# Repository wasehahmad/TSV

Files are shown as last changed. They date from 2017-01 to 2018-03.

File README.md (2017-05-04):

# TSV
Tractive System Voltage

This repository contains hardware and software for the PacMan (Pack Manager) and the AMS (Accumulator Management System)

Backup_pacman_software contains the software from the end of the 2016 project.

stable_software_20170413 contains the software on the packs at the end of the spring 2017 semester.

New_Pacman_Software contians the most recently tested software, with improvements added on to the stable_software.
Improvements include updated configuration parameters menus, power saving mode, and a lock mode that disables configutation
parameters to be edited.

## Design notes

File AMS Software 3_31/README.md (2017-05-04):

# LFEV Accumulator Mangement System (AMS)
This document describes the I2C interface to the AMS firmware, including the provided
functionality as well as how to test the boards outside of the pack. Also included is a brief
overview of how the software operates. 

## AMS I2C Interface

The following table describes the available functions in the current firmware revision.  
Included in the table is the command code as well as the I2C message structure:

### Command Code Description
| COMMAND | ENUM | DESCRIPTION |
|---|---|---|
| RESET_BY | 0x00 | Resets the bypass timer |
| SET_BY | 0x01 | Place device in bypass mode |
| PANIC | 0x02 | Rapidly blink LED |
| RELAX | 0x03 | End panic mode |
| SET_ADDR | 0x04 | Set device I2C address |
| SET_BYTIME | 0x05 | Set the bypass time |
| SET_V_CAL | 0x06 | Set the voltage calibration data |
| SET_SERIAL | 0x07 | Set the serial number |
| CHANGE_READ_TYPE  | 0x30 | Change the read type |

### API Documentation
#### RESET_BY: 0x00
This command resets the bypass timer within the device. If the bypass timer is not
reset before it counts up to the bypass limit, the device will begin discharging the battery in
bypass mode.
#### SET_BY: 0x01
This command directly sets the device into bypass mode.
PANIC: 0x02
This command sets the panic flag in the device. The panic flag does nothing more
than blink the “ACT” LED rapidly. None of the device functionality is affected.
#### RELAX: 0x03
This command disables the panic flag.

#### SET_ADDR: 0x04
This command sets the I2C address. The command word MUST be followed by
another byte to be set as the address. If this byte is not sent, the device can hang.

#### SET_BYTIME: 0x05
This command sets the bypass time limit for the device. The command word must be
followed by 2 bytes to act as the bypass time limit. These bytes must be sent MSB first. The
bypass time limit will be set to the given value multiplied by 32.8ms.
Reading data from the device:
To retrieve data from the device, an I2C read must be initiated for exactly 4 bytes. If
fewer or more bytes are read, the device can hang. The device will return two 16 bit values
representing the voltage and temperature respectively. The values will be transmitted MSB
first.

#### SET_V_CAL : 0x06
This command writes the calibration data to the AMS board's EEPROM. Four bytes of data 
should follow this command, two bytes for the slope, and two bytes for the offset. The 
high byte of the slope is sent first then the lower byte and the same process for the offset.

#### SET_SERIAL : 0x07
This command sets the 4-digit serial number for the AMS board. Four bytes of data should follow this 
command. Each digit in the serial number is sent individually beginning with the first digit.

#### CHANGE_READ_TYPE : 0x30
This command changes the read type for the AMS board. The board supports 4 different i2c reads. This 
command should be followed by another byte that dictates which read is to be performed: 
* for voltage/temp reading the next byte should be 0x00. 
* For the serial 0x01. 
* For the calibration data 0x02. 
* For the magic number 0x03.

## Device Programming and Testing
**The below guide has not been tested with the new version of the AMS software. It is recommended to connect
the AMS board to the Verifcation Unit for testing.**

To Program and test a device, you need a power supply capable of outputting at least
3 volts and 25 mA, a “PICKIT 3” programmer, and an “I2C2PC” adapter. A computer will be
needed with the PICKIT 3 software and RealTerm installed.
1. Attach the PICKIT 3 programmer to the AMS board.
2. Connect the AMS board to the power supply.
AMS Firmware Guide
3. Set the power supply to 3.3 volts with a limit of 1 A.
4. Enable power supply output. The voltage should settle to near 26mA.
AMS Firmware Guide
5. Connect the I2C2PC adapter to the I2C bus on the AMS board.
a. NOTE: The cable has been know to have connection issues. It may be necessary to check
the line voltage with an oscilloscope to ensure it can communicate with the bus.
6. Start PICKIT 3.
a. Select the file from the import dialog.
AMS Firmware Guide
b. Once the file has been imported, write it to the device.
7. Start RealTerm.
a. In the “Port” tab, select the I2C2PC adapter as the port (port 12, in this case).
b. Click “Change” to apply the change of settings.
8. Test basic I2C functionality by sending byte 0x00to address 0x04. The “ACT” LED
should blink once when the command is received.
AMS Firmware Guide
9. To test bypass mode, first increase the current limit of the power supply to 3A. This
time, send the packet 0x01.
a. The red “BYP” LED should light up and the current draw should increase to
2.9A.
b. Resend packet 0x00or reset the device to end bypass mode
10. Test the SET_ADDR command by sending the byte 0x04followed by the new I2C
address (here, it is 0x06) to change the address.
AMS Firmware Guide
a. Confirm the change in address by reading the EEPROM data in PICKIT 3
b. The data stored in location 0x00is the I2C address
11. Test the data retrieval by reading back 4 bytes from the device. The returned data
should reflect different voltage values if the supply voltage is changed between
iterations of this test.

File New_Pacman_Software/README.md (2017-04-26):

Lafayette College Formula Electric Vehicle

Pacman Software

This software controls the AT90CAN32 microcontroller located in the Lafayette Formula Electric Vehicle battery packs.  It is written in C and is built on AtomThreads RTOS.

The current version is v0.16 and has last been revised during the spring 2017 semester; the point of contact for this revision of software is Martin Townley.
Previous contributors to this software include Preston Bejabang and Geoff Nudge.

For documentation on this software, how to build and run it, the user manual and maintenace manual, please see http://sites.lafayette.edu/ece492-sp17/subsystems/tsv/

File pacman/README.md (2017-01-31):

# LFEV Pack Manager Main Board

## Overview

This directory contains the design of the LFEV "Packman" board. The "Packman" board, or
Pack Manager Board is responsible for monitoring the cells in the LFEV battery pack. This 
system contains a small AVR microprocessor capable of communicating high level data to the
SCADA system, while monitoring the pack for faults, managing cell charge/discharge, and tracking
the pack state of charge. This directory contains the PCB schematic and board layout
of the system.

## What's Here?

 - Kicad Project
     - Schematics
     - Board Layouts
     - Bill of Materials
 - Gerber Files
 - PDF Schematic

### Directory Structure

1. `Pacman_Rev_0_8` -- Contains versions of the finalized board layout, send these for fabrication
2. `project` -- KiCad project files... Open these to change the board design

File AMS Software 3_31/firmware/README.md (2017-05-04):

# AMS Firmware
Lafayette Formula Electric Vehicle Accumulator Mangement System Software

## Overview
This repository contains the PICLF1827 firmware. 

## Software Requirements
**OPTION A (Recommended)**
- Oracle VirtualBox

**OPTION B**
- MPLABX IDE 2.x or earlier
- MicroChip XC8 Compiler

### OPTION B: Oracle VirtualBox
The recommended way of building the system image is to use the pre-built VirtualBox environment. You will need to download VirtualBox, which can be found [here](https://www.virtualbox.org/wiki/Downloads).  

Go to the downloads page of the AMS repository, and download the latest virtual machine image. This image contains LXLE Ubuntu, and the MPLABX IDE and XC8 Compiler already installed. Simply mount the project folder on your host machine, and enable USB passthrough of the PICkit3 device.

### OPTION B: MicroChip MPLABX
This project was created using MicroChip proprietary IDE MPLABX. You can download a version of this IDE from [here](www.microchip.com/mplabx). However it should be noted that issues the PICkit3 and version 3.0 of the IDE may prevent programming of the PIC. A downgrade to version 2.x was required to successfully upload the software image.  
  
You will also need the MicroChip XC8 Compiler, which can be downloaded [here](www.microchip.com/compilers).

### Potential Problems
1. The PICkit3 has trouble with the MPLABX 3.x IDE, it complains that the firmware on the device is too old. Attempting to update the firmware either in the latest IDE, or an older one does not appear to have any effect.
2. If you are using the Virtual Machine Method, you must enable a USB Filter. Simply selecting Devices->USB Devices->PICkit3 is not enough. The PICkit3 re-uploads its firmware image upon each code upload. This causes the device to disconnect and re-connect itself. If a USB filter is not used, the host will take control of the PICkit3 immediately after it disconnects itself.

## Hardware Requirements
- PICkit3 Programmer

The PICkit3 Programmer is used to upload software images to the AMS microcontroller. The programmer can be purchased from MicroChip [Here](www.microchip.com/pickit3).

## Building the Image
Open MPLABX, click build... you're done

## Uploading the Image
Open MPLAB, click build, click program device... it should upload

If it did not upload verify that you have USB

##Additional Resources
Listed below are some additional resources for writing software for the AMS PIC.

### Power Saving Techniques
[PIC Microcontroller Low Power Techniques](http://ww1.microchip.com/downloads/en/DeviceDoc/01146B_chapter%202.pdf)

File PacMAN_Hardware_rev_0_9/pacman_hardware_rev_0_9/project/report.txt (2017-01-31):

Info: Reading netlist file "/home/strong/Documents/ECE492/pacman/pacman/hardware/main-board/project/pacman-main.net".

Info: Using references to match components and footprints.

* Warning: component 'T1': board footprint 'w_smd_inductors:transf_smd_ep7-8', netlist footprint 'custom_footprints:trans_flyback_LT8302'

* Warning: component 'Q2': board footprint 'w_smd_trans:sot23', netlist footprint 'custom_footprints:sot346'

* Warning: component 'Q1': board footprint 'w_smd_trans:sot23', netlist footprint 'custom_footprints:sot346'

* Warning: component 'U4': board footprint 'w_smd_dil:so-8', netlist footprint 'custom_footprints:msop_10_ads1015'

* Warning: component 'U5': board footprint 'Housings_SSOP:MSOP-10_3x3mm_Pitch0.5mm', netlist footprint 'custom_footprints:msop_10_ads1015'

* Warning: component 'D6': board footprint 'w_smd_diode:do214ac', netlist footprint 'custom_footprints:do214ac'

* Warning: component 'D5': board footprint 'w_smd_diode:do214ac', netlist footprint 'custom_footprints:do214ac'

* Warning: component 'D7': board footprint 'w_smd_diode:do214ac', netlist footprint 'custom_footprints:do214ac'

* Warning: component 'D8': board footprint 'w_smd_diode:do214ac', netlist footprint 'custom_footprints:do214ac'

* Warning: component 'D9': board footprint 'w_smd_diode:do214ac', netlist footprint 'custom_footprints:do214ac'

* Warning: component 'D18': board footprint 'w_smd_diode:do214ac', netlist footprint 'custom_footprints:do214ac'

* Warning: component 'D19': board footprint 'w_smd_diode:do214ac', netlist footprint 'custom_footprints:do214ac'

* Warning: component 'D15': board footprint 'w_smd_diode:do214ac', netlist footprint 'custom_footprints:do214ac'

* Warning: component 'X1': board footprint 'w_crystal:crystal_smd_5x3.2mm', netlist footprint 'custom_footprints:crystal_TXC_7A'

* Warning: component 'U13': board footprint 'w_smd_trans:tsot-6', netlist footprint 'custom_footprints:TLP2361'

* Warning: component 'SW1': board footprint 'w_switch:smd_push', netlist footprint 'custom_footprints:SW_RACON_8'

* Warning: component 'U10': board footprint 'w_smd_dil:mdip_6', netlist footprint 'custom_footprints:DCK'

* Warning: component 'R3': board footprint 'w_smd_resistors:r_0603', netlist footprint 'custom_footprints:CSNL1206'

* Warning: component 'F1': board footprint 'w_smd_resistors:r_1210', netlist footprint 'custom_footprints:C1Q'

* Warning: component 'P1': board footprint 'Connector_Molex_SL:molex_sl_smd_90_2', netlist footprint 'custom_footprints:AMPCONN_4POS'

* Warning: component 'U2': board footprint 'w_smd_trans:sot23-5', netlist footprint 'TO_SOT_Packages_SMD:SOT-23-5'

* Warning: component 'U9': board footprint 'w_smd_trans:sot223', netlist footprint 'TO_SOT_Packages_SMD:SOT-223'

* Warning: component 'R20': board footprint 'w_smd_resistors:r_0805', netlist footprint 'Resistors_SMD:R_0805_HandSoldering'

* Warning: component 'R19': board footprint 'w_smd_resistors:r_0805', netlist footprint 'Resistors_SMD:R_0805_HandSoldering'

* Warning: component 'R18': board footprint 'w_smd_resistors:r_0805', netlist footprint 'Resistors_SMD:R_0805_HandSoldering'

* Warning: component 'R25': board footprint 'w_smd_resistors:r_0805', netlist footprint 'Resistors_SMD:R_0805_HandSoldering'

* Warning: component 'R4': board footprint 'w_smd_resistors:r_0603', netlist footprint 'Resistors_SMD:R_0603_HandSoldering'

* Warning: component 'R30': board footprint 'w_smd_resistors:r_0603', netlist footprint 'Resistors_SMD:R_0603_HandSoldering'

* Warning: component 'R32': board footprint 'w_smd_resistors:r_0603', netlist footprint 'Resistors_SMD:R_0603_HandSoldering'

* Warning: component 'R31': board footprint 'w_smd_resistors:r_0603', netlist footprint 'Resistors_SMD:R_0603_HandSoldering'

* Warning: component 'R7': board footprint 'w_smd_resistors:r_0603', netlist footprint 'Resistors_SMD:R_0603_HandSoldering'

* Warning: component 'R6': board footprint 'w_smd_resistors:r_0603', netlist footprint 'Resistors_SMD:R_0603_HandSoldering'

* Warning: component 'R5': board footprint 'w_smd_resistors:r_0603', netlist footprint 'Resistors_SMD:R_0603_HandSoldering'

* Warning: component 'R37': board footprint 'w_smd_resistors:r_0603', netlist footprint 'Resistors_SMD:R_0603_HandSoldering'

* Warning: component 'R38': board footprint 'w_smd_resistors:r_0603', netlist footprint 'Resistors_SMD:R_0603_HandSoldering'

* Warning: component 'R23': board footprint 'w_smd_resistors:r_0603', netlist footprint 'Resistors_SMD:R_0603_HandSoldering'

* Warning: component 'R9': board footprint 'w_smd_resistors:r_0603', netlist footprint 'Resistors_SMD:R_0603_HandSoldering'

* Warning: component 'R24': board footprint 'w_smd_resistors:r_0603', netlist footprint 'Resistors_SMD:R_0603_HandSoldering'

* Warning: component 'R35': board footprint 'w_smd_resistors:r_0603', netlist footprint 'Resistors_SMD:R_0603_HandSoldering'

* Warning: component 'R36': board footprint 'w_smd_resistors:r_0603', netlist footprint 'Resistors_SMD:R_0603_HandSoldering'

* Warning: component 'R8': board footprint 'w_smd_resistors:r_0603', netlist footprint 'Resistors_SMD:R_0603_HandSoldering'

* Warning: component 'R14': board footprint 'w_smd_resistors:r_0603', netlist footprint 'Resistors_SMD:R_0603_HandSoldering'

* Warning: component 'R17': board footprint 'w_smd_resistors:r_0603', netlist footprint 'Resistors_SMD:R_0603_HandSoldering'

* Warning: component 'R16': board footprint 'w_smd_resistors:r_0603', netlist footprint 'Resistors_SMD:R_0603_HandSoldering'

* Warning: component 'R10': board footprint 'w_smd_resistors:r_0603', netlist footprint 'Resistors_SMD:R_0603_HandSoldering'

* Warning: component 'R34': board footprint 'w_smd_resistors:r_0603', netlist footprint 'Resistors_SMD:R_0603_HandSoldering'

* Warning: component 'R2': board footprint 'w_smd_resistors:r_0603', netlist footprint 'Resistors_SMD:R_0603_HandSoldering'

* Warning: component 'R15': board footprint 'w_smd_resistors:r_0603', netlist footprint 'Resistors_SMD:R_0603_HandSoldering'

* Warning: component 'R13': board footprint 'w_smd_resistors:r_0603', netlist footprint 'Resistors_SMD:R_0603_HandSoldering'

* Warning: component 'R1': board footprint 'w_smd_resistors:r_0603', netlist footprint 'Resistors_SMD:R_0603_HandSoldering'

* Warning: component 'D3': board footprint 'w_smd_leds:Led_0603', netlist footprint 'LEDs:LED_0603'

* Warning: component 'D12': board footprint 'w_smd_leds:Led_0603', netlist footprint 'LEDs:LED_0603'

* Warning: component 'D2': board footprint 'w_smd_leds:Led_0603', netlist footprint 'LEDs:LED_0603'

* Warning: component 'D1': board footprint 'w_smd_leds:Led_0603', netlist footprint 'LEDs:LED_0603'

* Warning: component 'U3': board footprint 'w_smd_dil:soic-16', netlist footprint 'Housings_SOIC:SOIC-16_7.5x10.3mm_Pitch1.27mm'

* Warning: component 'P4': board footprint 'w_conn_strip:vasch_strip_8x2', netlist footprint 'Connect:IDC_Header_Straight_16pins'

* Warning: component 'C16': board footprint 'w_smd_cap:c_elec_6.3x7.7', netlist footprint 'Capacitors_SMD:c_elec_6.3x7.7'

* Warning: component 'C10': board footprint 'w_smd_cap:c_elec_10x10', netlist footprint 'Capacitors_SMD:c_elec_10x10'

* Warning: component 'C11': board footprint 'w_smd_cap:c_1210', netlist footprint 'Capacitors_SMD:C_1210_HandSoldering'

* Warning: component 'C15': board footprint 'w_smd_cap:c_1210', netlist footprint 'Capacitors_SMD:C_1210_HandSoldering'

* Warning: component 'C9': board footprint 'w_smd_cap:c_1210', netlist footprint 'Capacitors_SMD:C_1210_HandSoldering'

* Warning: component 'C14': board footprint 'w_smd_cap:c_0805', netlist footprint 'Capacitors_SMD:C_0805'

* Warning: component 'C2': board footprint 'w_smd_cap:c_0603', netlist footprint 'Capacitors_SMD:C_0603_HandSoldering'

* Warning: component 'C18': board footprint 'w_smd_cap:c_0603', netlist footprint 'Capacitors_SMD:C_0603_HandSoldering'

* Warning: component 'C12': board footprint 'w_smd_cap:c_0603', netlist footprint 'Capacitors_SMD:C_0603_HandSoldering'

* Warning: component 'C21': board footprint 'w_smd_cap:c_0603', netlist footprint 'Capacitors_SMD:C_0603_HandSoldering'

* Warning: component 'C8': board footprint 'w_smd_cap:c_0603', netlist footprint 'Capacitors_SMD:C_0603_HandSoldering'

* Warning: component 'C20': board footprint 'w_smd_cap:c_0603', netlist footprint 'Capacitors_SMD:C_0603_HandSoldering'

* Warning: component 'C19': board footprint 'w_smd_cap:c_0603', netlist footprint 'Capacitors_SMD:C_0603_HandSoldering'

* Warning: component 'C7': board footprint 'w_smd_cap:c_1210', netlist footprint 'Capacitors_SMD:C_0603_HandSoldering'

* Warning: component 'C13': board footprint 'w_smd_cap:c_0603', netlist footprint 'Capacitors_SMD:C_0603_HandSoldering'

* Warning: component 'C17': board footprint 'w_smd_cap:c_0603', netlist footprint 'Capacitors_SMD:C_0603_HandSoldering'

* Warning: component 'C1': board footprint 'w_smd_cap:c_0603', netlist footprint 'Capacitors_SMD:C_0603_HandSoldering'

* Warning: component 'C4': board footprint 'w_smd_cap:c_0603', netlist footprint 'Capacitors_SMD:C_0603_HandSoldering'

* Warning: component 'C6': board footprint 'w_smd_cap:c_0603', netlist footprint 'Capacitors_SMD:C_0603_HandSoldering'

* Warning: component 'C3': board footprint 'w_smd_cap:c_0603', netlist footprint 'Capacitors_SMD:C_0603_HandSoldering'

* Warning: component 'C5': board footprint 'w_smd_cap:c_0603', netlist footprint 'Capacitors_SMD:C_0603_HandSoldering'

* Warning: component 'C23': board footprint 'w_smd_cap:c_0603', netlist footprint 'Capacitors_SMD:C_0603_HandSoldering'

* Warning: component 'C22': board footprint 'w_smd_cap:c_0603', netlist footprint 'Capacitors_SMD:C_0603_HandSoldering'

Info: Checking netlist component footprint "C1:/5572610D:Capacitors_SMD:C_0603_HandSoldering".

Info: Checking netlist component footprint "C2:/557225A0:Capacitors_SMD:C_0603_HandSoldering".

Info: Checking netlist component footprint "C3:/5572D9B1:Capacitors_SMD:C_0603_HandSoldering".

Info: Checking netlist component footprint "C4:/55726574:Capacitors_SMD:C_0603_HandSoldering".

Info: Checking netlist component footprint "C5:/5572DAEA:Capacitors_SMD:C_0603_HandSoldering".

Info: Checking netlist component footprint "C6:/55727969:Capacitors_SMD:C_0603_HandSoldering".

Info: Checking netlist component footprint "C7:/560A91B4/56DA9A93:Capacitors_SMD:C_0603_HandSoldering".

Info: Checking netlist component footprint "C8:/5574E706/561A469B:Capacitors_SMD:C_0603_HandSoldering".

Info: Checking netlist component footprint "C9:/5574E706/5574EF4E:Capacitors_SMD:C_1210_HandSoldering".

Info: Checking netlist component footprint "C10:/5574E706/56149C59:Capacitors_SMD:c_elec_10x10".

Info: Checking netlist component footprint "C11:/5574E706/560E8698:Capacitors_SMD:C_1210_HandSoldering".

Info: Checking netlist component footprint "C12:/5574E706/5574EF55:Capacitors_SMD:C_0603_HandSoldering".

Info: Checking netlist component footprint "C13:/5574E706/559EAEEF:Capacitors_SMD:C_0603_HandSoldering".

Info: Checking netlist component footprint "C14:/5574E706/561A342C:Capacitors_SMD:C_0805".

Info: Checking netlist component footprint "C15:/5574E706/560EA637:Capacitors_SMD:C_1210_HandSoldering".

Info: Checking netlist component footprint "C16:/5574E706/5574EF8D:Capacitors_SMD:c_elec_6.3x7.7".

Info: Checking netlist component footprint "C17:/5574E706/559EB3D2:Capacitors_SMD:C_0603_HandSoldering".

Info: Checking netlist component footprint "C18:/5574E706/5574EFA4:Capacitors_SMD:C_0603_HandSoldering".

Info: Checking netlist component footprint "C19:/561EAC87/561EE3E1:Capacitors_SMD:C_0603_HandSoldering".

Info: Checking netlist component footprint "C20:/560D7137/560D7928:Capacitors_SMD:C_0603_HandSoldering".

Info: Checking netlist component footprint "C21:/560D7137/560D79A3:Capacitors_SMD:C_0603_HandSoldering".

Info: Checking netlist component footprint "C22:/5574E706/56251D56:Capacitors_SMD:C_0603_HandSoldering".

Info: Checking netlist component footprint "C23:/5574E706/56252980:Capacitors_SMD:C_0603_HandSoldering".

Info: Checking netlist component footprint "C24:/5574E706/56C84061:Capacitors_SMD:C_0603_HandSoldering".

Info: Checking netlist component footprint "D1:/5572956F:LEDs:LED_0603".

Info: Checking netlist component footprint "D2:/557296B7:LEDs:LED_0603".

Info: Checking netlist component footprint "D3:/55735E6E:LEDs:LED_0603".

Info: Checking netlist component footprint "D5:/5574E706/5614A4E6:custom_footprints:do214ac".

Info: Checking netlist component footprint "D6:/5574E706/560E9E47:custom_footprints:do214ac".

Info: Checking netlist component footprint "D7:/5574E706/561A26BD:custom_footprints:do214ac".

Info: Checking netlist component footprint "D8:/5574E706/561F00F0:custom_footprints:do214ac".

Info: Checking netlist component footprint "D9:/5574E706/561F2090:custom_footprints:do214ac".

Info: Checking netlist component footprint "D12:/560A91B4/560D901A:LEDs:LED_0603".

Info: Checking netlist component footprint "D15:/560D7137/5618023D:custom_footprints:do214ac".

Info: Checking netlist component footprint "D18:/560A91B4/562AB319:custom_footprints:do214ac".

Info: Checking netlist component footprint "D19:/560A91B4/562B02FC:custom_footprints:do214ac".

Info: Checking netlist component footprint "D20:/5574E706/56C84F96:footprints:sod123".

Info: Checking netlist component footprint "D21:/560A91B4/56C97FC6:custom_footprints:do214ac".

Info: Checking netlist component footprint "F1:/5574E706/56D7F3E2:custom_footprints:C1Q".

Info: Checking netlist component footprint "J1:/5623433E/56153025:custom_footprints:conn_usb_B".

Info: Checking netlist component footprint "J2:/5623433E/56260A54:Connect:DB37FD".

Info: Checking netlist component footprint "J3:/5623433E/56CD8443:custom_footprints:MOLEX_RJ11".

Info: Checking netlist component footprint "L1:/5574E706/560E9174:Inductors:SELF-WE-TPC_M".

Info: Checking netlist component footprint "P1:/5623433E/56D7CCD6:custom_footprints:AMPCONN_4POS".

Info: Checking netlist component footprint "P2:/5623433E/562C320E:Connector_Molex_SL:molex_sl_smd_90_2".

Info: Checking netlist component footprint "P3:/5623433E/56151585:Connector_Molex_SL:molex_sl_smd_90_6".

Info: Checking netlist component footprint "P4:/5623433E/5623747B:Connect:IDC_Header_Straight_16pins".

Info: Checking netlist component footprint "P5:/5623433E/5615226C:Connector_1-27mm:JTAG_10ARM".

Info: Checking netlist component footprint "Q1:/560A91B4/562ABB38:custom_footprints:sot346".

Info: Checking netlist component footprint "Q2:/560A91B4/56D1463E:custom_footprints:sot346".

Info: Checking netlist component footprint "Q3:/560A91B4/56D0EFAD:custom_footprints:sot346".

Info: Checking netlist component footprint "Q4:/5574E706/56DA35B2:custom_footprints:sot346".

Info: Checking netlist component footprint "R1:/561E7314:Resistors_SMD:R_0603_HandSoldering".

Info: Checking netlist component footprint "R2:/561E731A:Resistors_SMD:R_0603_HandSoldering".

Info: Checking netlist component footprint "R3:/5574E706/56D7B790:custom_footprints:CSNL1206".

Info: Checking netlist component footprint "R4:/560A91B4/56D86223:Resistors_SMD:R_0603_HandSoldering".

Info: Checking netlist component footprint "R5:/55716F3C:Resistors_SMD:R_0603_HandSoldering".

Info: Checking netlist component footprint "R6:/55729155:Resistors_SMD:R_0603_HandSoldering".

Info: Checking netlist component footprint "R7:/55729416:Resistors_SMD:R_0603_HandSoldering".

Info: Checking netlist component footprint "R8:/55735E62:Resistors_SMD:R_0603_HandSoldering".

Info: Checking netlist component footprint "R9:/560A91B4/56DAA10E:Resistors_SMD:R_0603_HandSoldering".

Info: Checking netlist component footprint "R10:/5574E706/5617C752:Resistors_SMD:R_0603_HandSoldering".

Info: Checking netlist component footprint "R13:/5574E706/561427CD:Resistors_SMD:R_0603_HandSoldering".

Info: Checking netlist component footprint "R14:/5574E706/56148A93:Resistors_SMD:R_0603_HandSoldering".

Info: Checking netlist component footprint "R15:/5574E706/561A10DD:Resistors_SMD:R_0603_HandSoldering".

Info: Checking netlist component footprint "R16:/5574E706/5614AFEA:Resistors_SMD:R_0603_HandSoldering".

Info: Checking netlist component footprint "R17:/5574E706/5614A4DF:Resistors_SMD:R_0603_HandSoldering".

Info: Checking netlist component footprint "R18:/5574E706/561A34B4:Resistors_SMD:R_0805_HandSoldering".

Info: Checking netlist component footprint "R19:/5574E706/56135999:Resistors_SMD:R_0805_HandSoldering".

Info: Checking netlist component footprint "R20:/5574E706/5613543A:Resistors_SMD:R_0805_HandSoldering".

Info: Checking netlist component footprint "R23:/560A91B4/560D9022:Resistors_SMD:R_0603_HandSoldering".

Info: Checking netlist component footprint "R24:/561EAC87/561EE3D3:Resistors_SMD:R_0603_HandSoldering".

Info: Checking netlist component footprint "R25:/561EAC87/561EE3CB:Resistors_SMD:R_0805_HandSoldering".

Info: Checking netlist component footprint "R30:/5574E706/563343E2:Resistors_SMD:R_0603_HandSoldering".

Info: Checking netlist component footprint "R31:/5574E706/563371CA:Resistors_SMD:R_0603_HandSoldering".

Info: Checking netlist component footprint "R32:/5574E706/56336F03:Resistors_SMD:R_0603_HandSoldering".

Info: Checking netlist component footprint "R34:/5629F005:Resistors_SMD:R_0603_HandSoldering".

Info: Checking netlist component footprint "R35:/5623433E/562BA965:Resistors_SMD:R_0603_HandSoldering".

Info: Checking netlist component footprint "R36:/5623433E/562BAD35:Resistors_SMD:R_0603_HandSoldering".

Info: Checking netlist component footprint "R37:/560A91B4/562A49C0:Resistors_SMD:R_0603_HandSoldering".

Info: Checking netlist component footprint "R38:/560A91B4/562A59DB:Resistors_SMD:R_0603_HandSoldering".

Info: Checking netlist component footprint "RLY1:/560A91B4/56C8F931:custom_footprints:relay_G5LE_1A4".

Info: Checking netlist component footprint "RLY2:/560A91B4/56DBD4FE:custom_footprints:RLY_T9AS1D12-5".

Info: Checking netlist component footprint "SW1:/55715F36:custom_footprints:SW_RACON_8".

Info: Checking netlist component footprint "T1:/5574E706/557BAF56:custom_footprints:trans_flyback_LT8302".

Info: Checking netlist component footprint "U1:/55247ABB:Housings_QFP:TQFP-64_14x14mm_Pitch0.8mm".

Info: Checking netlist component footprint "U2:/558A42AE:TO_SOT_Packages_SMD:SOT-23-5".

Info: Checking netlist component footprint "U3:/5574E706/560B0C11:Housings_SOIC:SOIC-16_7.5x10.3mm_Pitch1.27mm".

Info: Checking netlist component footprint "U4:/5574E706/56D798E2:custom_footprints:msop_10_ads1015".

Info: Checking netlist component footprint "U5:/5574E706/56C794D3:custom_footprints:msop_10_ads1015".

Info: Checking netlist component footprint "U6:/5574E706/560E8451:custom_footprints:TSSOP16_LTC3638".

Info: Checking netlist component footprint "U7:/5574E706/56145C36:custom_footprints:SOIC-8-1EP_3.9x4.9mm_Pitch1.27mm".

Info: Checking netlist component footprint "U8:/5574E706/559EAA55:Housings_SOIC:SOIC-8_3.9x4.9mm_Pitch1.27mm".

Info: Checking netlist component footprint "U9:/5574E706/5574EF3F:TO_SOT_Packages_SMD:SOT-223".

Info: Checking netlist component footprint "U10:/560A91B4/56D82DAA:custom_footprints:DCK".

Info: Checking netlist component footprint "U11:/561EAC87/561EE3B4:Housings_SOIC:SOIC-8_3.9x4.9mm_Pitch1.27mm".

Info: Checking netlist component footprint "U12:/560D7137/560D798D:Housings_SSOP:SSOP-28_5.3x10.2mm_Pitch0.65mm".

Info: Checking netlist component footprint "U13:/560A91B4/56DA73C4:custom_footprints:TLP2361".

Info: Checking netlist component footprint "X1:/55722FB6:custom_footprints:crystal_TXC_7A".

Error: Component 'J3' pad '8' not found in footprint 'custom_footprints:MOLEX_RJ11'

Error: Component 'J3' pad '7' not found in footprint 'custom_footprints:MOLEX_RJ11'

Error: Component 'P1' pad '3' not found in footprint 'Connector_Molex_SL:molex_sl_smd_90_2'

Error: Component 'P1' pad '4' not found in footprint 'Connector_Molex_SL:molex_sl_smd_90_2'

Error: Component 'U4' pad '10' not found in footprint 'w_smd_dil:so-8'

Error: Component 'U4' pad '9' not found in footprint 'w_smd_dil:so-8'

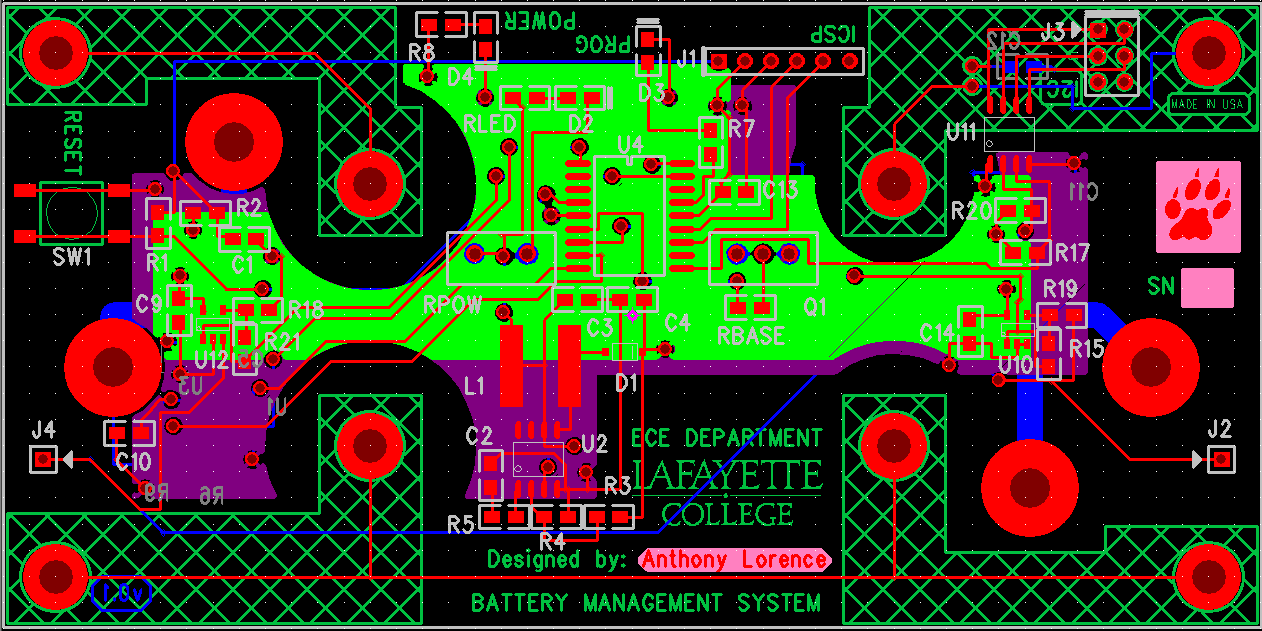
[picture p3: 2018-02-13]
AMS_hardware/EDAWork/PCB/PADSlayout.PNG

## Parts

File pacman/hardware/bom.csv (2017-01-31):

Reference | Value | Footprint | Datasheet | Supplier | Supplier P/N | Supplier URL | Manufacturer | Manufacturer P/N | Datasheet URL | Description | Unit Cost | Digikey | Manufacturer URL
C2 | 0.1u | w_smd_cap:c_0603
X1 | 10MHz | w_crystal:crystal_smd_5x3.2mm |  | Digikey | 887-1741-1-ND | http://www.digikey.com/product-search/en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 | TXC Corporation | 7A-10.000MAAE-T | http://www.mouser.com/ds/2/417/7a-13881.pdf | 10MHz SMD Crystal | 0.72
C1 | 10p | w_smd_cap:c_0603
C4 | 10p | w_smd_cap:c_0603
C6 | 0.1u | w_smd_cap:c_0603
SW1 | RESET | w_switch:smd_push
R5 | 10k | w_smd_resistors:r_0603
C3 | 0.1u | w_smd_cap:c_0603
C5 | 0.1u | w_smd_cap:c_0603
R6 | 1k | w_smd_resistors:r_0603
R7 | 1k | w_smd_resistors:r_0603
D1 | POWER | w_smd_leds:Led_0603 |  |  |  |  |  |  |  | 0603 LED (BLUE)
D2 | FAULT | w_smd_leds:Led_0603 |  |  |  |  |  |  |  | 0603 LED (RED)
R8 | 1k | w_smd_resistors:r_0603
D3 | REQUEST | w_smd_leds:Led_0603 |  |  |  |  |  |  |  | 0603 LED (YELLOW)
R9 | 1k | w_smd_resistors:r_0603
D4 | LOW VOLT | w_smd_leds:Led_0603 |  |  |  |  |  |  |  | 0603 LED (YELLOW)
U1 | AT90CAN32-M | Housings_QFP:TQFP-64_14x14mm_Pitch0.8mm |  | Digikey | AT90CAN32-16AURCT-ND | http://www.digikey.com/product-detail/en/AT90CAN32-16AUR/AT90CAN32-16AURCT-ND/3789385 | Atmel | AT90CAN32-16AUR | http://www.atmel.com/Images/7679s.pdf | IC MCU 8BIT 32KB FLASH 64TQFP | 7.52
U2 | ADM6320 | w_smd_trans:sot23-5 |  | Digikey | ADM6320CY29ARJZ-R7CT-ND | http://www.digikey.com/product-detail/en/ADM6320CY29ARJZ-R7/ADM6320CY29ARJZ-R7CT-ND/2467999 | Analog Devices | ADM6320CY29ARJZ-R7 | http://www.mouser.com/ds/2/609/ADM6316_6317_6318_6319_6320_6321_6322-259224.pdf | External Watchdog IC 2.9V 1600mS 140mS | 1.52
R3 | 10k | w_smd_resistors:r_0603
R4 | 10k | w_smd_resistors:r_0603
R1 | 10k | w_smd_resistors:r_0603
R2 | 10k | w_smd_resistors:r_0603
R34 | 10k | w_smd_resistors:r_0603
U9 | NCP1117ST33T3G | w_smd_trans:sot223 |  | Digikey | NCP1117ST33T3GOSCT-ND | http://www.digikey.com/product-detail/en/NCP1117ST33T3G/NCP1117ST33T3GOSCT-ND/660708 | ON Semiconductor | NCP1117ST33T3G | http://www.onsemi.com/pub_link/Collateral/NCP1117-D.PDF | IC REG LDO 3.3V 1A SOT223 | 0.49
C16 | 220u | w_smd_cap:c_elec_6.3x7.7 |  | Digikey | 493-6214-1-ND | http://www.digikey.com/product-search/en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 | Nichicon | UUR1C221MCL6GS |  | SMD 16volts 220uF 20% 85C 6.3X7.7 | 0.41
C18 | 0.1u | w_smd_cap:c_0603
U8 | Si8600 | Housings_SOIC:SOIC-8_3.9x4.9mm_Pitch1.27mm |  | Digikey | SI8600AC-B-ISR-ND | http://www.digikey.com/product-detail/en/SI8600AC-B-ISR/SI8600AC-B-ISR-ND/4069772 | Silicon Labs | Si8600AC-B-IS | http://www.silabs.com/Support%20Documents/TechnicalDocs/Si860x.pdf | 3.75kV Bidirect I2C Isolator 1.7MHz | 2.96
C13 | 0.1u | w_smd_cap:c_0603
C17 | 0.1u | w_smd_cap:c_0603
U3 | PCF8574A | w_smd_dil:soic-16 |  | Digikey | 568-1074-1-ND | http://www.digikey.com/product-detail/en/PCF8574AT%2F3518/568-1074-1-ND/735790 | NXP Semiconductors | PCF8574AT3518 | http://www.nxp.com/documents/data_sheet/PCF8574_PCF8574A.pdf | IC I/O EXPANDER I2C 8B 16SOIC | 1.22
U6 | LTC3638 | custom_footprints:TSSOP16_LTC3638 |  | Digikey | LTC3638EMSE#PBF-ND | http://www.digikey.com/product-detail/en/LTC3638EMSE%23PBF/LTC3638EMSE%23PBF-ND/4693775 | Linear Technology | LTC3638EMSE#PBF | http://www.linear.com/docs/44312 | IC REG BUCK ADJ 0.25A 16MSOP | 7.79
C11 | 10u | w_smd_cap:c_1210 |  | Digikey | 490-1891-1-ND | http://www.digikey.com/product-detail/en/GRM32DF51H106ZA01L/490-1891-1-ND/587282 | Murata Electronics | GRM32DF51H106ZA01L | http://search.murata.co.jp/Ceramy/image/img/A01X/G101/ENG/GRM32DF51H106ZA01-01.pdf | CAP CER 10UF 50V Y5V 1210 | 0.61
L1 | 220u | Inductors:SELF-WE-TPC_M |  | Digikey | 445-173047-1-ND | http://www.digikey.com/product-detail/en/VLS6045EX-221M/445-173047-1-ND/5287389 | TDK Corporation | VLS6045EX-221M | http://product.tdk.com/en/catalog/datasheets/inductor_commercial_power_vls6045ex_en.pdf | FIXED IND 220UH 500MA 1.15 MOHM | 0.52
D6 | SK310A-LTP | w_smd_diode:do214ac |  | Digikey | SK310A-LTPMSCT-ND | http://www.digikey.com/product-detail/en/SK310A-LTP/SK310A-LTPMSCT-ND/2642066 | Micro Commercial Components (MMC) | SK310A-LTP | http://www.mccsemi.com/up_pdf/SK32A-LT~SK310A-LT%28DO-214AC%29.PDF | Schottky Diodes & Rectifiers DIODE SCHOTTKY 100V 3A DO214AC | 0.57
C15 | 10u | w_smd_cap:c_1210 |  | Digikey | 490-1891-1-ND | http://www.digikey.com/product-detail/en/GRM32DF51H106ZA01L/490-1891-1-ND/587282 | Murata Electronics | GRM32DF51H106ZA01L | http://search.murata.co.jp/Ceramy/image/img/A01X/G101/ENG/GRM32DF51H106ZA01-01.pdf | CAP CER 10UF 50V Y5V 1210 | 0.61
C9 | 10u | w_smd_cap:c_1210 |  | Digikey | 490-1891-1-ND | http://www.digikey.com/product-detail/en/GRM32DF51H106ZA01L/490-1891-1-ND/587282 | Murata Electronics | GRM32DF51H106ZA01L | http://search.murata.co.jp/Ceramy/image/img/A01X/G101/ENG/GRM32DF51H106ZA01-01.pdf | CAP CER 10UF 50V Y5V 1210 | 0.61
C12 | 1u | w_smd_cap:c_0603
R20 | 10k | w_smd_resistors:r_0805
R19 | 10k | w_smd_resistors:r_0805
U4 | MCP6402 | w_smd_dil:so-8 |  | Digikey | MCP6402-E/SN-ND | http://www.digikey.com/product-detail/en/MCP6402-E%2FSN/MCP6402-E%2FSN-ND/2385853 | Microchip Technology | MCP6402-E/SN | http://www.mouser.com/ds/2/268/22229b-13594.pdf | Op Amps Dual 1.8V 1MHz | 0.44
R12 | 100K 1% | w_smd_resistors:r_0805
C7 | 10u | w_smd_cap:c_1210 |  | Digikey | 490-1891-1-ND | http://www.digikey.com/product-detail/en/GRM32DF51H106ZA01L/490-1891-1-ND/587282 | Murata Electronics | GRM32DF51H106ZA01L | http://search.murata.co.jp/Ceramy/image/img/A01X/G101/ENG/GRM32DF51H106ZA01-01.pdf | CAP CER 10UF 50V Y5V 1210 | 0.61
R11 | 1M 1% | w_smd_resistors:r_0805
U5 | ADS1013 | Housings_SSOP:MSOP-10_3x3mm_Pitch0.5mm |  | Digikey | 296-25225-1-ND | http://www.digikey.com/product-search/en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 | Texas Instruments | ADS1013IDGST | http://www.ti.com/lit/ds/symlink/ads1013.pdf | IC ADC 12BIT I2C W/REF 10-MSOP | 3.13
C8 | 0.1u | w_smd_cap:c_0603
R13 | 1M 1% | w_smd_resistors:r_0603
R14 | 300K 1% | w_smd_resistors:r_0603
R17 | 158K 1% | w_smd_resistors:r_0603
R16 | 10K | w_smd_resistors:r_0603
C10 | 220u | w_smd_cap:c_elec_10x10 |  | Digikey | 493-9426-1-ND | http://www.digikey.com/product-detail/en/UCW1H221MNL1GS/493-9426-1-ND/3962774 | Nichion | UCW1H221MNL1GS |  | CAP ALUM 220UF 20% 50V SMD | 0.79
D5 | SK310A-LTP | w_smd_diode:do214ac |  | Digikey | SK310A-LTPMSCT-ND | http://www.digikey.com/product-detail/en/SK310A-LTP/SK310A-LTPMSCT-ND/2642066 | Micro Commercial Components (MMC) | SK310A-LTP | http://www.mccsemi.com/up_pdf/SK32A-LT~SK310A-LT%28DO-214AC%29.PDF | Schottky Diodes & Rectifiers DIODE SCHOTTKY 100V 3A DO214AC | 0.57
T1 | WURTH_750311564 | w_smd_inductors:transf_smd_ep7-8 |  | Digikey | 1297-1132-1-ND | http://www.digikey.com/product-detail/en/750313441/1297-1132-1-ND/4959521 | Wurth Electronics | 750313441 | http://katalog.we-online.de/ctm/datasheet/750313441.pdf | TRANS FLYBACK LT8302 | 4.55
R15 | 113K 1% | w_smd_resistors:r_0603
D7 | PTZTE2533B | w_smd_diode:do214ac |  | Digikey | PTZTE2533BCT-ND | http://www.digikey.com/product-detail/en/PTZTE2533B/PTZTE2533BCT-ND/3443738 | Rohm Semiconductor | PTZTE2533B | http://rohmfs.rohm.com/en/products/databook/datasheet/discrete/diode/zener/ptz33b.pdf | DIODE ZENER 35V 1W PMDS | 0.45
C14 | 220p | w_smd_cap:c_0805
R18 | 10K | w_smd_resistors:r_0805
D8 | SK310A-LTP | w_smd_diode:do214ac |  |  | SK310A-LTPMSCT-ND | http://www.digikey.com/product-detail/en/SK310A-LTP/SK310A-LTPMSCT-ND/2642066 | Micro Commercial Components (MMC) | SK310A-LTP | http://www.mccsemi.com/up_pdf/SK32A-LT~SK310A-LT%28DO-214AC%29.PDF | Schottky Diodes & Rectifiers DIODE SCHOTTKY 100V 3A DO214AC | 0.57 | Mouser
D9 | SK310A-LTP | w_smd_diode:do214ac |  | Digikey | SK310A-LTPMSCT-ND | http://www.digikey.com/product-detail/en/SK310A-LTP/SK310A-LTPMSCT-ND/2642066 | Micro Commercial Components (MMC) | SK310A-LTP | http://www.mccsemi.com/up_pdf/SK32A-LT~SK310A-LT%28DO-214AC%29.PDF | Schottky Diodes & Rectifiers DIODE SCHOTTKY 100V 3A DO214AC | 0.57
U7 | LT8302 | custom_footprints:SOIC-8-1EP_3.9x4.9mm_Pitch1.27mm |  | Digikey | LT8302ES8E#PBF-ND | http://www.digikey.com/product-detail/en/LT8302ES8E%23PBF/LT8302ES8E%23PBF-ND/4488938 | Linear Technology | LT8302ES8E#PBF | http://cds.linear.com/docs/en/datasheet/8302fa.pdf | IC REG FLYBCK INV ISO 3.6A 8SOIC | 7.41
R10 | 10k | w_smd_resistors:r_0603
R30 | 0 1% | w_smd_resistors:r_0603
R32 | 10M 1% | w_smd_resistors:r_0603
R31 | 0 1% | w_smd_resistors:r_0603
C22 | 0.1u | w_smd_cap:c_0603
C23 | 0.1u | w_smd_cap:c_0603
D12 | CHARGE | w_smd_leds:Led_0603 |  |  |  |  |  |  |  | 0603 LED (GREEN)
R23 | 1k | w_smd_resistors:r_0603
U10 | RELAY_VO14642AT | w_smd_dil:mdip_6 |  | Digikey | VO14642AT-ND | http://www.digikey.com/product-search/en?keywords=VO14642AT | Vishay Semiconductors | VO14642AT | http://www.vishay.com/docs/81646/vo14642a.pdf | Solid State Relay NO 1A 60V | 2.66
D10 | SAFE | w_smd_leds:Led_0603 |  |  |  |  |  |  |  | 0603 LED (GREEN)
R21 | 1k | w_smd_resistors:r_0603
D11 | ERROR | w_smd_leds:Led_0603 |  |  |  |  |  |  |  | 0603 LED (GREEN)
R22 | 1k | w_smd_resistors:r_0603
R33 | 1k | w_smd_resistors:r_0603
U13 | 74LVC2G07 | w_smd_trans:tsot-6 |  | Digikey | 568-4617-1-ND | http://www.digikey.com/product-detail/en/74LVC2G07GW125/568-4617-1-ND/1965412 | NXP Semiconductors | 74LVC2G07GW125 | http://www.nxp.com/documents/data_sheet/74LVC2G07.pdf | IC BUFFER N-INV OP/DRAIN 6TSSOP | 0.45
D18 | SK310A-LTP | w_smd_diode:do214ac |  | Digikey | SK310A-LTPMSCT-ND | http://www.digikey.com/product-detail/en/SK310A-LTP/SK310A-LTPMSCT-ND/2642066 | Micro Commercial Components (MMC) | SK310A-LTP | http://www.mccsemi.com/up_pdf/SK32A-LT~SK310A-LT%28DO-214AC%29.PDF | Schottky Diodes & Rectifiers DIODE SCHOTTKY 100V 3A DO214AC | 0.57
Q1 | SI2323DDS | w_smd_trans:sot23 |  | Digikey | SI2371EDS-T1-GE3CT-ND | http://www.digikey.com/product-detail/en/SI2371EDS-T1-GE3/SI2371EDS-T1-GE3CT-ND/4142087 | Vishay Siliconix | SI2371EDS-T1-GE3 | http://www.vishay.com/docs/64004/si2323dds.pdf | MOSFET P-CH 30V 4.8A SOT-23 | 0.42
Q2 | SI2323DDS | w_smd_trans:sot23 |  | Digikey | SI2371EDS-T1-GE3CT-ND | http://www.digikey.com/product-detail/en/SI2371EDS-T1-GE3/SI2371EDS-T1-GE3CT-ND/4142087 | Vishay Siliconix | SI2371EDS-T1-GE3 | http://www.vishay.com/docs/64004/si2323dds.pdf | MOSFET P-CH 30V 4.8A SOT-23 | 0.42
D19 | SK310A-LTP | w_smd_diode:do214ac |  | Digikey | SK310A-LTPMSCT-ND | http://www.digikey.com/product-detail/en/SK310A-LTP/SK310A-LTPMSCT-ND/2642066 | Micro Commercial Components (MMC) | SK310A-LTP | http://www.mccsemi.com/up_pdf/SK32A-LT~SK310A-LT%28DO-214AC%29.PDF | Schottky Diodes & Rectifiers DIODE SCHOTTKY 100V 3A DO214AC | 0.57
R37 | 10k | w_smd_resistors:r_0603
R38 | 10k | w_smd_resistors:r_0603
U11 | MCP2551-I/SN | Housings_SOIC:SOIC-8_3.9x4.9mm_Pitch1.27mm |  | Digikey | MCP2551-I/SN-ND | http://www.digikey.com/product-search/en?keywords=MCP2551-I%2FSN | Microchip | MCP2551-I/SN | http://ww1.microchip.com/downloads/en/DeviceDoc/21667f.pdf | CAN Interface IC | 1.02 |  | http://www.microchip.com/wwwproducts/Devices.aspx?dDocName=en010405
R25 | 120 | w_smd_resistors:r_0805
R24 | 1k | w_smd_resistors:r_0603
C19 | 0.1u | w_smd_cap:c_0603
D13 | CANTX | w_smd_leds:Led_0603 |  |  |  |  |  |  |  | 0603 LED (RED)
D14 | CANRX | w_smd_leds:Led_0603 |  |  |  |  |  |  |  | 0603 LED (YELLOW)
R26 | 1k | w_smd_resistors:r_0603
R27 | 1k | w_smd_resistors:r_0603
C20 | 0.1u | w_smd_cap:c_0603
D16 | TX | w_smd_leds:Led_0603 |  |  |  |  |  |  |  | 0603 LED (RED)
D17 | RX | w_smd_leds:Led_0603 |  |  |  |  |  |  |  | 0603 LED (YELLOW)
R28 | 1k | w_smd_resistors:r_0603
R29 | 1k | w_smd_resistors:r_0603
U12 | FT232RL | Housings_SSOP:SSOP-28_5.3x10.2mm_Pitch0.65mm |  | Digikey | 768-1007-1-ND | http://www.digikey.com/product-detail/en/FT232RL-REEL/768-1007-1-ND/1836402 | FTDI | FT232RL-REEL | http://www.ftdichip.com/Support/Documents/DataSheets/ICs/DS_FT232R.pdf | IC USB FS SERIAL UART 28-SSOP | 4.5
C21 | 0.1u | w_smd_cap:c_0603
F1 | 500mA | w_smd_resistors:r_1210 |  | Digikey | F2998CT-ND | http://www.digikey.com/product-search/en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 | Littelfuse | 1210L050YR |  | 500mA PTC Fuse | 0.51
D15 | SK310A-LTP | w_smd_diode:do214ac |  | Digikey | SK310A-LTPMSCT-ND | http://www.digikey.com/product-detail/en/SK310A-LTP/SK310A-LTPMSCT-ND/2642066 | Micro Commercial Components (MMC) | SK310A-LTP | http://www.mccsemi.com/up_pdf/SK32A-LT~SK310A-LT%28DO-214AC%29.PDF | Schottky Diodes & Rectifiers DIODE SCHOTTKY 100V 3A DO214AC | 0.57
J1 | USB | custom_footprints:conn_usb_B |  | Digikey | A114945-ND | http://www.digikey.com/product-detail/en/1734346-1/A114945-ND/1891565 | TE Connectivity | 1734346-1 | http://www.te.com/catalog/pn/en/1734346-1?RQPN=1734346-1 | USB Connectors B Blk 4pos R/A SMT | 1.36
P5 | JTAG | Connector_1-27mm:JTAG_10ARM |  | Digikey | 609-4054-ND | http://www.digikey.com/product-detail/en/20021521-00010T1LF/609-4054-ND/2414951 | FCI | 20021521-00010T1LF | http://portal.fciconnect.com/Comergent//fci/drawing/20021521.pdf | Headers & Wire Housings 10P STRT 4WALL GLDFL | 1.1
P1 | BATTERY | Connector_Molex_SL:molex_sl_smd_90_2 |  | Digikey | WM1340-ND | http://www.digikey.com/product-search/en?keywords=15-91-2025 | Molex | 15-91-2025 | http://www.mouser.com/ds/2/276/0015912025_PCB_HEADERS-227317.pdf | Headers 2.54 WIRE/BOARD HDR Right Angle 2 CKT | 2.61
P3 | EXT I2C | Connector_Molex_SL:molex_sl_smd_90_6 |  | Digikey | WM1344-ND | http://www.digikey.com/product-search/en?keywords=15-91-2065 | Molex | 15-91-2065 |  | Headers & Wire Housings 2.54 WIRE/BOARD HDR Right Angle 6 CKT | 4.2 |  | http://www.molex.com/molex/products/datasheet.jsp?part=active/0015912065_PCB_HEADERS.xml
P4 | GPIO | w_conn_strip:vasch_strip_8x2 |  | Digikey | 3M11931-ND | http://www.digikey.com/product-search/en?keywords=30316-6002HB | 3M | 30316-6002HB | http://www.mouser.com/ds/2/1/TS0818-221281.pdf | Headers & Wire Housings 26P STRT 4WALL GLDFL | 0.78
J2 | BACKPLANE CONNECTOR | Connect:DB37FD |  | Digikey | 5237FE-ND | http://www.digikey.com/product-detail/en/171-037-213R011/5237FE-ND/858167 | Norcomp Inc | 171-037-213R011 |  | D-Sub Connector Receptacle Female Sockets 37 Position Through Hole Solder | 3.88
R35 | 100 | w_smd_resistors:r_0603
R36 | 100 | w_smd_resistors:r_0603
P2 | DETECT | Connector_Molex_SL:molex_sl_smd_90_2 |  | Digikey | WM1340-ND | http://www.digikey.com/product-search/en?keywords=15-91-2025 | Molex | 15-91-2025 | http://www.mouser.com/ds/2/276/0015912025_PCB_HEADERS-227317.pdf | Headers 2.54 WIRE/BOARD HDR Right Angle 2 CKT | 2.61

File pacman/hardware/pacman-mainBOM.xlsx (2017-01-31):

Reference | Value | Supplier | Supplier P/N | Manufacturer | Manufacturer P/N | Description | Unit Cost
C2 | 0.1u
X1 | 10MHz | Digikey | 887-1741-1-ND | TXC Corporation | 7A-10.000MAAE-T | 10MHz SMD Crystal | 0.72
C1 | 10p
C4 | 10p
C6 | 0.1u
SW1 | RESET | Digikey | CKN9363CT-ND | C&K Components | 1.14100.5030000 | SWITCH PUSH SPST-NO 0.1A 42V | 2.43
R5 | 10k
C3 | 0.1u
C5 | 0.1u
R6 | 1k
R7 | 1k
D1 | POWER |  |  |  |  | 0603 LED (BLUE)
D2 | FAULT |  |  |  |  | 0603 LED (RED)
U1 | AT90CAN128-M | Digikey | AT90CAN128-16AURCT-ND | Atmel | AT90CAN128-16AUR | IC MCU 8BIT 128KB FLASH 64TQFP | 10.4
U2 | ADM6320 | Digikey | ADM6320CY29ARJZ-R7CT-ND | Analog Devices | ADM6320CY29ARJZ-R7 | External Watchdog IC 2.9V 1600mS 140mS | 1.52
R1 | 10k
R2 | 10k
R34 | 10k
D3 | SPARE |  |  |  |  | 0603 LED (BLUE)
R8 | 1k
U9 | NCP1117ST33T3G | Digikey | NCP1117ST33T3GOSCT-ND | ON Semiconductor | NCP1117ST33T3G | IC REG LDO 3.3V 1A SOT223 | 0.49
C16 | 220u | Digikey | 493-6214-1-ND | Nichicon | UUR1C221MCL6GS | SMD 16volts 220uF 20% 85C 6.3X7.7 | 0.41
C18 | 0.1u
U8 | Si8600 | Digikey | SI8600AC-B-ISR-ND | Silicon Labs | Si8600AC-B-IS | 3.75kV Bidirect I2C Isolator 1.7MHz | 2.96
C13 | 0.1u
C17 | 0.1u
U3 | PCF8574A | Digikey | 568-1074-1-ND | NXP Semiconductors | PCF8574AT3518 | IC I/O EXPANDER I2C 8B 16SOIC | 1.22
U6 | LTC3638 | Digikey | LTC3638EMSE#PBF-ND | Linear Technology | LTC3638EMSE#PBF | IC REG BUCK ADJ 0.25A 16MSOP | 7.79
C11 | 10u | Digikey | 490-1891-1-ND | Murata Electronics | GRM32DF51H106ZA01L | CAP CER 10UF 50V Y5V 1210 | 0.61
L1 | 220u | Digikey | 445-173047-1-ND | TDK Corporation | VLS6045EX-221M | FIXED IND 220UH 500MA 1.15 MOHM | 0.52
D6 | SK310A-LTP | Digikey | SK310A-LTPMSCT-ND | Micro Commercial Components (MMC) | SK310A-LTP | Schottky Diodes & Rectifiers DIODE SCHOTTKY 100V 3A DO214AC | 0.57
C15 | 10u | Digikey | 490-1891-1-ND | Murata Electronics | GRM32DF51H106ZA01L | CAP CER 10UF 50V Y5V 1210 | 0.61
C9 | 10u | Digikey | 490-1891-1-ND | Murata Electronics | GRM32DF51H106ZA01L | CAP CER 10UF 50V Y5V 1210 | 0.61
C12 | 1u
R20 | 10k
R19 | 10k
C8 | 0.1u
R13 | 1M 1%
R14 | 300K 1%
R17 | 115K 1%
R16 | 10K 1%
C10 | 220u | Digikey | 493-9426-1-ND | Nichion | UCW1H221MNL1GS | CAP ALUM 220UF 20% 50V SMD | 0.79
D5 | SK310A-LTP | Digikey | SK310A-LTPMSCT-ND | Micro Commercial Components (MMC) | SK310A-LTP | Schottky Diodes & Rectifiers DIODE SCHOTTKY 100V 3A DO214AC | 0.57
T1 | WURTH_750311564 | Digikey | 1297-1132-1-ND | Wurth Electronics | 750313441 | TRANS FLYBACK LT8302 | 4.55
R15 | 113K 1%
D7 | PTZTE2533B | Digikey | PTZTE2533BCT-ND | Rohm Semiconductor | PTZTE2533B | DIODE ZENER 35V 1W PMDS | 0.45
C14 | 220p
R18 | 10K
D8 | SK310A-LTP | Digikey | SK310A-LTPMSCT-ND | Micro Commercial Components (MMC) | SK310A-LTP | Schottky Diodes & Rectifiers DIODE SCHOTTKY 100V 3A DO214AC | 0.57
D9 | SK310A-LTP | Digikey | SK310A-LTPMSCT-ND | Micro Commercial Components (MMC) | SK310A-LTP | Schottky Diodes & Rectifiers DIODE SCHOTTKY 100V 3A DO214AC | 0.57
U7 | LT8302 | Digikey | LT8302ES8E#PBF-ND | Linear Technology | LT8302ES8E#PBF | IC REG FLYBCK INV ISO 3.6A 8SOIC | 7.41
R10 | 10k
R30 | 0 1%
R32 | 10M 1%
R31 | 0 1%
C22 | 0.1u
C23 | 0.1u
U5 | ADS1115 | Digikey | 296-38849-1-ND | Texas Instruments | ADS1115IDGSR | IC ADC 16BIT 860SPS LP 10MSOP | 5.65
C24 | 0.1u | Digikey | ?
D20 | NZH5V1B | Digikey | 568-6370-1-ND | NXP Semiconductors | NZH5V1B | DIODE ZENER 5.1V 500MW SOD123F | 0.2
U4 | INA_226 | Digikey | 296-29034-1-ND | Texas Instruments | INA226AIDGSR |  | 3.44
R3 | 0.001 1% | Digikey | CSNL1206FT1L00CT-ND | Stackpole Electronics | CSNL1206FT1L00 | RES SMD 0.001 OHM 1% 1W 1206 | 0.65
F1 | FUSE | Digikey | 507-1077-1-ND | Bel Fuse Inc | C1Q 1 | FUSE BOARD MOUNT 1A 125VAC 63VDC | 0.31
Q4 | RRR015P03TL | Digikey | RRR015P03TLCT-ND | Rohm Semiconductor | RRR015P03TL | MOSFET P-CH 30V 1.5A TSMT3 | 0.43
R11 | 10k
D12 | CHARGE |  |  |  |  | 0603 LED (GREEN)
R23 | 1k
D18 | SK310A-LTP | Digikey | SK310A-LTPMSCT-ND | Micro Commercial Components (MMC) | SK310A-LTP | Schottky Diodes & Rectifiers DIODE SCHOTTKY 100V 3A DO214AC | 0.57
Q1 | RRR015P03TL | Digikey | RRR015P03TLCT-ND | Rohm Semiconductor | RRR015P03TL | MOSFET P-CH 30V 1.5A TSMT3 | 0.43
D19 | SK310A-LTP | Digikey | SK310A-LTPMSCT-ND | Micro Commercial Components (MMC) | SK310A-LTP | Schottky Diodes & Rectifiers DIODE SCHOTTKY 100V 3A DO214AC | 0.57
R37 | 10k
R38 | 10k
RLY1 | G5LE-1A4 DC3 | Digikey | Z3697-ND | Omron | G5LE-1A4 DC3 | RELAY GEN PURPOSE SPST 10A 3V | 1.43
D21 | SK310A-LTP | Digikey | SK310A-LTPMSCT-ND | Micro Commercial Components (MMC) | SK310A-LTP | Schottky Diodes & Rectifiers DIODE SCHOTTKY 100V 3A DO214AC | 0.57
Q3 | RRR015P03TL | Digikey | RRR015P03TLCT-ND | Rohm Semiconductor | RRR015P03TL | MOSFET P-CH 30V 1.5A TSMT3 | 0.43
Q2 | RRR015P03TL | Digikey | RRR015P03TLCT-ND | Rohm Semiconductor | RRR015P03TL | MOSFET P-CH 30V 1.5A TSMT3 | 0.43
U10 | SN74LVC2G06 | Digikey | 296-13493-1-ND | Texas Instruments | SN74LVC2G06DCKR | IC INVERTER DUAL 1INPUT SC706 | 0.54
R4 | 1k
U13 | TLP2361 | Digikey | TLP2361(V4-TPLECT-ND | Toshiba Semiconductor and Storage | TLP2361(V4-TPL | OPTOISO 3.75KV PSH PULL SO6-5 | 1.14
C7 | 0.1u
R9 | 10k
RLY2 | T9AS1D12-5 | Digikey | PB1014-ND | TE Connectivity Potter & Brumfield Relays | T9AS1D12-5 | RELAY GEN PURPOSE SPST 30A 5V | 4.22
U11 | MCP2551-I/SN | Digikey | MCP2551-I/SN-ND | Microchip | MCP2551-I/SN | CAN Interface IC | 1.02
R25 | 120
R24 | 1k
C19 | 0.1u
C20 | 0.1u
U12 | FT232RL | Digikey | 768-1007-1-ND | FTDI | FT232RL-REEL | IC USB FS SERIAL UART 28-SSOP | 4.5
C21 | 0.1u
D15 | SK310A-LTP | Digikey | SK310A-LTPMSCT-ND | Micro Commercial Components (MMC) | SK310A-LTP | Schottky Diodes & Rectifiers DIODE SCHOTTKY 100V 3A DO214AC | 0.57
J1 | USB | Digikey | A114945-ND | TE Connectivity | 1734346-1 | USB Connectors B Blk 4pos R/A SMT | 1.36
P5 | JTAG | Digikey | 609-4054-ND | FCI | 20021521-00010T1LF | Headers & Wire Housings 10P STRT 4WALL GLDFL | 1.1
P3 | EXT I2C | Digikey | WM1344-ND | Molex | 15-91-2065 | Headers & Wire Housings 2.54 WIRE/BOARD HDR Right Angle 6 CKT | 4.2
P4 | GPIO | Digikey | 3M11931-ND | 3M | 30316-6002HB | Headers & Wire Housings 26P STRT 4WALL GLDFL | 0.78
J2 | BACKPLANE CONNECTOR | Digikey | 5237FE-ND | Norcomp Inc | 171-037-213R011 | D-Sub Connector Receptacle Female Sockets 37 Position Through Hole Solder | 3.88
R35 | 100
R36 | 100
P2 | CDETECT | Digikey | WM1340-ND | Molex | 15-91-2025 | Headers 2.54 WIRE/BOARD HDR Right Angle 2 CKT | 2.61
J3 | RJ12 | Digikey | WM3789CT-ND | Molex LLC | 855135002 | CONN MOD JACK 6P6C VERT UNSHLD | 1.16
P1 | POWER | Digikey | A113982-ND | TE Connectivity AMP Connectors | 556881-4 | CONN RCPT 4POS 11.18MM PCB SLDR | 8.66
R12 | 100
R21 | 100
P6 | LDETECT | Digikey | WM1340-ND | Molex | 15-91-2025 | Headers 2.54 WIRE/BOARD HDR Right Angle 2 CKT | 2.61

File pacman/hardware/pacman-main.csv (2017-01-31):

Reference | Value | Footprint | Datasheet | Supplier | Supplier P/N | Supplier URL | Manufacturer | Manufacturer P/N | Datasheet URL | Description | Unit Cost | Accessory | Supplier URl | Manufacturer URL | NOTE
C2 | 0.1u | Capacitors_SMD:C_0603_HandSoldering
X1 | 10MHz | custom_footprints:crystal_TXC_7A |  | Digikey | 887-1741-1-ND | http://www.digikey.com/product-search/en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 | TXC Corporation | 7A-10.000MAAE-T | http://www.mouser.com/ds/2/417/7a-13881.pdf | 10MHz SMD Crystal | 0.72
C1 | 10p | Capacitors_SMD:C_0603_HandSoldering |  | DigiKey | 490-6112-1-ND | http://www.digikey.com/product-detail/en/murata-electronics-north-america/GRM0335C1H100JA01D/490-6112-1-ND/3845312 | Murata Electronics North America | GRM0335C1H100JA01D | http://www.murata.com/~/media/webrenewal/support/library/catalog/products/capacitor/mlcc/c02e.pdf | 10pF 50V Ceramic Capacitor C0G | NP0 0201 (0603 Metric) 0.024" L x 0.012" W (0.60mm x 0.30mm) | 0.10
C4 | 10p | Capacitors_SMD:C_0603_HandSoldering |  | DigiKey | 490-6112-1-ND | http://www.digikey.com/product-detail/en/murata-electronics-north-america/GRM0335C1H100JA01D/490-6112-1-ND/3845312 | Murata Electronics North America | GRM0335C1H100JA01D | http://www.murata.com/~/media/webrenewal/support/library/catalog/products/capacitor/mlcc/c02e.pdf | 10pF 50V Ceramic Capacitor C0G | NP0 0201 (0603 Metric) 0.024" L x 0.012" W (0.60mm x 0.30mm) | 0.10
C6 | 0.1u | Capacitors_SMD:C_0603_HandSoldering
SW1 | RESET | custom_footprints:SW_RACON_8 |  | Digikey | CKN9363CT-ND | http://www.digikey.com/product-detail/en/c-k-components/1.14100.5030000/CKN9363CT-ND/583462 | C&K Components | 1.14100.5030000 | http://www.ck-components.com/43191/short-travel-racon.pdf/ | SWITCH PUSH SPST-NO 0.1A 42V | 2.43
C3 | 0.1u | Capacitors_SMD:C_0603_HandSoldering
C5 | 0.1u | Capacitors_SMD:C_0603_HandSoldering
R6 | 1k | Resistors_SMD:R_0603_HandSoldering
R7 | 1k | Resistors_SMD:R_0603_HandSoldering
D1 | POWER | LEDs:LED_0603 |  |  |  |  |  |  |  | 0603 LED (BLUE)
D2 | FAULT | LEDs:LED_0603 |  |  |  |  |  |  |  | 0603 LED (RED)
U1 | AT90CAN128-M | Housings_QFP:TQFP-64_14x14mm_Pitch0.8mm |  | Digikey | AT90CAN128-16AURCT-ND | http://www.digikey.com/product-detail/en/atmel/AT90CAN128-16AUR/AT90CAN128-16AURCT-ND/3789383 | Atmel | AT90CAN128-16AUR | http://www.atmel.com/Images/7679s.pdf | IC MCU 8BIT 128KB FLASH 64TQFP | 10.40
U2 | ADM6320 | TO_SOT_Packages_SMD:SOT-23-5 |  | Digikey | ADM6320CY29ARJZ-R7CT-ND | http://www.digikey.com/product-detail/en/ADM6320CY29ARJZ-R7/ADM6320CY29ARJZ-R7CT-ND/2467999 | Analog Devices | ADM6320CY29ARJZ-R7 | http://www.mouser.com/ds/2/609/ADM6316_6317_6318_6319_6320_6321_6322-259224.pdf | External Watchdog IC 2.9V 1600mS 140mS | 1.52
R1 | 10k | Resistors_SMD:R_0603_HandSoldering
R2 | 10k | Resistors_SMD:R_0603_HandSoldering
R34 | 10k | Resistors_SMD:R_0603_HandSoldering
D3 | SPARE | LEDs:LED_0603 |  |  |  |  |  |  |  | 0603 LED (BLUE)
R8 | 1k | Resistors_SMD:R_0603_HandSoldering
C18 | 0.1u | Capacitors_SMD:C_0603_HandSoldering |  | DigiKey | 490-1524-1-ND | http://www.digikey.com/product-detail/en/murata-electronics-north-america/GRM188R71E104KA01D/490-1524-1-ND/587865 | Murata Electronics North America | GRM188R71E104KA01D | http://search.murata.co.jp/Ceramy/image/img/A01X/G101/ENG/GRM188R71E104KA01-01.pdf | 0.10µF 25V Ceramic Capacitor X7R 0603 (1608 Metric) 0.063" L x 0.031" W (1.60mm x 0.80mm) | 0.10
C26 | 0.1u | Capacitors_SMD:C_0603_HandSoldering |  | DigiKey | 490-1524-1-ND | http://www.digikey.com/product-detail/en/murata-electronics-north-america/GRM188R71E104KA01D/490-1524-1-ND/587865 | Murata Electronics North America | GRM188R71E104KA01D | http://search.murata.co.jp/Ceramy/image/img/A01X/G101/ENG/GRM188R71E104KA01-01.pdf | 0.10µF 25V Ceramic Capacitor X7R 0603 (1608 Metric) 0.063" L x 0.031" W (1.60mm x 0.80mm) | 0.10
U9 | NCP1117ST33T3G | TO_SOT_Packages_SMD:SOT-223 |  | Digikey | NCP1117ST33T3GOSCT-ND | http://www.digikey.com/product-detail/en/NCP1117ST33T3G/NCP1117ST33T3GOSCT-ND/660708 | ON Semiconductor | NCP1117ST33T3G | http://www.onsemi.com/pub_link/Collateral/NCP1117-D.PDF | IC REG LDO 3.3V 1A SOT223 | 0.49
C16 | 220u | Capacitors_SMD:c_elec_6.3x7.7 |  | Digikey | 493-6214-1-ND | http://www.digikey.com/product-search/en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 | Nichicon | UUR1C221MCL6GS |  | SMD 16volts 220uF 20% 85C 6.3X7.7 | .41
U8 | Si8600 | Housings_SOIC:SOIC-8_3.9x4.9mm_Pitch1.27mm |  | Digikey | 336-2048-5-ND | http://www.digikey.com/product-detail/en/silicon-labs/SI8600AC-B-IS/336-2048-5-ND/2623281 | Silicon Labs | Si8600AC-B-IS | http://www.silabs.com/Support%20Documents/TechnicalDocs/Si860x.pdf | 3.75kV Bidirect I2C Isolator 1.7MHz | 2.96
C13 | 0.1u | Capacitors_SMD:C_0603_HandSoldering
C17 | 0.1u | Capacitors_SMD:C_0603_HandSoldering
U3 | PCF8574A | Housings_SOIC:SOIC-16_7.5x10.3mm_Pitch1.27mm |  | Digikey | 568-1074-1-ND | http://www.digikey.com/product-detail/en/PCF8574AT%2F3518/568-1074-1-ND/735790 | NXP Semiconductors | PCF8574AT3518 | http://www.nxp.com/documents/data_sheet/PCF8574_PCF8574A.pdf | IC I/O EXPANDER I2C 8B 16SOIC | 1.22
U6 | LTC3638 | custom_footprints:TSSOP16_LTC3638 |  | Digikey | LTC3638EMSE#PBF-ND | http://www.digikey.com/product-detail/en/LTC3638EMSE%23PBF/LTC3638EMSE%23PBF-ND/4693775 | Linear Technology | LTC3638EMSE#PBF | http://www.linear.com/docs/44312 | IC REG BUCK ADJ 0.25A 16MSOP | 7.79
C11 | 1u | Capacitors_SMD:C_0603_HandSoldering |  | Digikey | 490-1891-1-ND | http://www.digikey.com/product-detail/en/GRM32DF51H106ZA01L/490-1891-1-ND/587282 | Murata Electronics | GRM32DF51H106ZA01L | http://search.murata.co.jp/Ceramy/image/img/A01X/G101/ENG/GRM32DF51H106ZA01-01.pdf | CAP CER 10UF 50V Y5V 1210 | 0.61
L1 | 220u | Inductors:SELF-WE-TPC_M |  | Digikey | 445-173047-1-ND | http://www.digikey.com/product-detail/en/VLS6045EX-221M/445-173047-1-ND/5287389 | TDK Corporation | VLS6045EX-221M | http://product.tdk.com/en/catalog/datasheets/inductor_commercial_power_vls6045ex_en.pdf | FIXED IND 220UH 500MA 1.15 MOHM | 0.52
D6 | SK310A-LTP | custom_footprints:do214ac |  | Digikey | SK310A-LTPMSCT-ND | http://www.digikey.com/product-detail/en/SK310A-LTP/SK310A-LTPMSCT-ND/2642066 | Micro Commercial Components (MMC) | SK310A-LTP | http://www.mccsemi.com/up_pdf/SK32A-LT~SK310A-LT%28DO-214AC%29.PDF | Schottky Diodes & Rectifiers DIODE SCHOTTKY 100V 3A DO214AC | 0.57
C15 | 10u | Capacitors_SMD:C_1210_HandSoldering |  | Digikey | 490-1891-1-ND | http://www.digikey.com/product-detail/en/GRM32DF51H106ZA01L/490-1891-1-ND/587282 | Murata Electronics | GRM32DF51H106ZA01L | http://search.murata.co.jp/Ceramy/image/img/A01X/G101/ENG/GRM32DF51H106ZA01-01.pdf | CAP CER 10UF 50V Y5V 1210 | 0.61
R20 | 1k | Resistors_SMD:R_0805_HandSoldering
R19 | 1k | Resistors_SMD:R_0805_HandSoldering
C8 | 0.1u | Capacitors_SMD:C_0603_HandSoldering
C10 | 220u | Capacitors_SMD:c_elec_10x10 |  | Digikey | 493-9426-1-ND | http://www.digikey.com/product-detail/en/UCW1H221MNL1GS/493-9426-1-ND/3962774 | Nichion | UCW1H221MNL1GS |  | CAP ALUM 220UF 20% 50V SMD | 0.79
D5 | SK310A-LTP | custom_footprints:do214ac |  | Digikey | SK310A-LTPMSCT-ND | http://www.digikey.com/product-detail/en/SK310A-LTP/SK310A-LTPMSCT-ND/2642066 | Micro Commercial Components (MMC) | SK310A-LTP | http://www.mccsemi.com/up_pdf/SK32A-LT~SK310A-LT%28DO-214AC%29.PDF | Schottky Diodes & Rectifiers DIODE SCHOTTKY 100V 3A DO214AC | 0.57
D9 | SK310A-LTP | custom_footprints:do214ac |  | Digikey | SK310A-LTPMSCT-ND | http://www.digikey.com/product-detail/en/SK310A-LTP/SK310A-LTPMSCT-ND/2642066 | Micro Commercial Components (MMC) | SK310A-LTP | http://www.mccsemi.com/up_pdf/SK32A-LT~SK310A-LT%28DO-214AC%29.PDF | Schottky Diodes & Rectifiers DIODE SCHOTTKY 100V 3A DO214AC | 0.57
R10 | 10k | Resistors_SMD:R_0603_HandSoldering
C22 | 0.1u | Capacitors_SMD:C_0603_HandSoldering
C23 | 0.1u | Capacitors_SMD:C_0603_HandSoldering
U5 | ADS1115 | custom_footprints:msop_10_ads1015 |  | Digikey | 296-38849-1-ND | http://www.digikey.com/product-detail/en/texas-instruments/ADS1115IDGSR/296-38849-1-ND/5142969 | Texas Instruments | ADS1115IDGSR | http://www.ti.com/lit/ds/symlink/ads1113.pdf | IC ADC 16BIT 860SPS LP 10MSOP | 5.65
C24 | 0.1u | Capacitors_SMD:C_0603_HandSoldering |  | Digikey | ?
D20 | NZH5V1B | footprints:sod123 |  | Digikey | 568-6370-1-ND | http://www.digikey.com/product-detail/en/NZH5V1B115/568-6370-1-ND/2531657 | NXP Semiconductors | NZH5V1B | http://www.nxp.com/documents/data_sheet/NZH_SER.pdf | DIODE ZENER 5.1V 500MW SOD123F | 0.20
U4 | INA_226 | custom_footprints:msop_10_ads1015 |  | Digikey | 296-29034-1-ND | http://www.digikey.com/product-search/en?keywords=296-29034-1-ND | Texas Instruments | INA226AIDGSR | http://www.ti.com/lit/ds/symlink/ina226.pdf |  | 3.44
R3 | 0.001 1% | custom_footprints:CSNL1206 |  | Digikey | CSNL1206FT1L00CT-ND | http://www.digikey.com/product-detail/en/stackpole-electronics-inc/CSNL1206FT1L00/CSNL1206FT1L00CT-ND/1788120 | Stackpole Electronics | CSNL1206FT1L00 | https://www.seielect.com/Catalog/SEI-csnl.pdf | RES SMD 0.001 OHM 1% 1W 1206 | 0.65
F1 | 5 A | custom_footprints:blade_fuse_holder |  | Digikey | BK-6010-ND | http://www.digikey.com/product-detail/en/mpd-memory-protection-devices/BK-6010/BK-6010-ND/2330529 | Memory Protection Devices | BK-6010 | http://www.memoryprotectiondevices.com/datasheets/BK-6010-datasheet.pdf | FUSE BLOCK BLADE PCB | 0.54 | 5A Blade Fuse
Q4 | RRR015P03TL | custom_footprints:sot346 |  | Digikey | RRR015P03TLCT-ND | http://www.digikey.com/product-detail/en/RRR015P03TL/RRR015P03TLCT-ND/3769397 | Rohm Semiconductor | RRR015P03TL | http://rohmfs.rohm.com/en/products/databook/datasheet/discrete/transistor/mosfet/rrr015p03tl-e.pdf | MOSFET P-CH 30V 1.5A TSMT3 | 0.43
R11 | 10k | Resistors_SMD:R_0603_HandSoldering
R13 | 1 1% | Resistors_SMD:R_0805_HandSoldering
C12 | 10u | Capacitors_SMD:C_1210_HandSoldering |  | Digikey | 490-1891-1-ND | http://www.digikey.com/product-detail/en/GRM32DF51H106ZA01L/490-1891-1-ND/587282 | Murata Electronics | GRM32DF51H106ZA01L | http://search.murata.co.jp/Ceramy/image/img/A01X/G101/ENG/GRM32DF51H106ZA01-01.pdf | CAP CER 10UF 50V Y5V 1210 | 0.61
R14 | 1k | Resistors_SMD:R_0805_HandSoldering
U7 | NCS6S1205C | custom_footprints:NCS6S1205C |  | Digikey | 811-2109-5-ND |  | Murata | NCS6S1205C | http://power.murata.com/data/power/ncl/kdc_ncs6.pdf | CONVERT DC/DC 6W 12VIN-5VOUT T/H | 22.00 |  | http://power.murata.com/data/power/ncl/kdc_ncs6.pdf
C9 | 10u | Capacitors_SMD:C_1210_HandSoldering |  | Digikey | 490-1891-1-ND | http://www.digikey.com/product-detail/en/GRM32DF51H106ZA01L/490-1891-1-ND/587282 | Murata Electronics | GRM32DF51H106ZA01L | http://search.murata.co.jp/Ceramy/image/img/A01X/G101/ENG/GRM32DF51H106ZA01-01.pdf | CAP CER 10UF 50V Y5V 1210 | 0.61
C25 | 0.1u | Capacitors_SMD:C_0603_HandSoldering
C14 | 0.1u | Capacitors_SMD:C_0603_HandSoldering
C27 | 10u | Capacitors_SMD:C_1210_HandSoldering |  | Digikey | 490-1891-1-ND | http://www.digikey.com/product-detail/en/GRM32DF51H106ZA01L/490-1891-1-ND/587282 | Murata Electronics | GRM32DF51H106ZA01L | http://search.murata.co.jp/Ceramy/image/img/A01X/G101/ENG/GRM32DF51H106ZA01-01.pdf | CAP CER 10UF 50V Y5V 1210 | 0.61
D12 | CHARGE | LEDs:LED_0603 |  |  |  |  |  |  |  | 0603 LED (GREEN)
R23 | 1k | Resistors_SMD:R_0603_HandSoldering
D18 | SK310A-LTP | custom_footprints:do214ac |  | Digikey | SK310A-LTPMSCT-ND | http://www.digikey.com/product-detail/en/SK310A-LTP/SK310A-LTPMSCT-ND/2642066 | Micro Commercial Components (MMC) | SK310A-LTP | http://www.mccsemi.com/up_pdf/SK32A-LT~SK310A-LT%28DO-214AC%29.PDF | Schottky Diodes & Rectifiers DIODE SCHOTTKY 100V 3A DO214AC | 0.57
Q1 | RRR015P03TL | custom_footprints:sot346 |  | Digikey | RRR015P03TLCT-ND | http://www.digikey.com/product-detail/en/RRR015P03TL/RRR015P03TLCT-ND/3769397 | Rohm Semiconductor | RRR015P03TL | http://rohmfs.rohm.com/en/products/databook/datasheet/discrete/transistor/mosfet/rrr015p03tl-e.pdf | MOSFET P-CH 30V 1.5A TSMT3 | 0.43
D19 | SK310A-LTP | custom_footprints:do214ac |  | Digikey | SK310A-LTPMSCT-ND | http://www.digikey.com/product-detail/en/SK310A-LTP/SK310A-LTPMSCT-ND/2642066 | Micro Commercial Components (MMC) | SK310A-LTP | http://www.mccsemi.com/up_pdf/SK32A-LT~SK310A-LT%28DO-214AC%29.PDF | Schottky Diodes & Rectifiers DIODE SCHOTTKY 100V 3A DO214AC | 0.57
R37 | 10k | Resistors_SMD:R_0603_HandSoldering
R38 | 10k | Resistors_SMD:R_0603_HandSoldering
RLY1 | G5LE-1A4 DC3 | custom_footprints:relay_G5LE_1A4 |  | Digikey | Z3697-ND | http://www.digikey.com/product-detail/en/G5LE-1A4%20DC3/Z3697-ND/1815639 | Omron | G5LE-1A4 DC3 | https://www.components.omron.com/components/web/PDFLIB.nsf/0/0293ACA6B03161CD86257538007424DB/$file/G5LE_0813.pdf | RELAY GEN PURPOSE SPST 10A 3V | 1.43
D21 | SK310A-LTP | custom_footprints:do214ac |  | Digikey | SK310A-LTPMSCT-ND | http://www.digikey.com/product-detail/en/SK310A-LTP/SK310A-LTPMSCT-ND/2642066 | Micro Commercial Components (MMC) | SK310A-LTP | http://www.mccsemi.com/up_pdf/SK32A-LT~SK310A-LT%28DO-214AC%29.PDF | Schottky Diodes & Rectifiers DIODE SCHOTTKY 100V 3A DO214AC | 0.57
Q3 | RRR015P03TL | custom_footprints:sot346 |  | Digikey | RRR015P03TLCT-ND | http://www.digikey.com/product-detail/en/RRR015P03TL/RRR015P03TLCT-ND/3769397 | Rohm Semiconductor | RRR015P03TL | http://rohmfs.rohm.com/en/products/databook/datasheet/discrete/transistor/mosfet/rrr015p03tl-e.pdf | MOSFET P-CH 30V 1.5A TSMT3 | 0.43
Q2 | RRR015P03TL | custom_footprints:sot346 |  | Digikey | RRR015P03TLCT-ND | http://www.digikey.com/product-detail/en/RRR015P03TL/RRR015P03TLCT-ND/3769397 | Rohm Semiconductor | RRR015P03TL | http://rohmfs.rohm.com/en/products/databook/datasheet/discrete/transistor/mosfet/rrr015p03tl-e.pdf | MOSFET P-CH 30V 1.5A TSMT3 | 0.43
U10 | SN74LVC2G06 | custom_footprints:DCK |  | Digikey | 296-13493-1-ND | http://www.digikey.com/product-detail/en/texas-instruments/SN74LVC2G06DCKR/296-13493-1-ND/486425 | Texas Instruments | SN74LVC2G06DCKR | http://www.ti.com/lit/ds/symlink/sn74lvc2g06.pdf | IC INVERTER DUAL 1INPUT SC706 | 0.54
R4 | 510 | Resistors_SMD:R_0603_HandSoldering |  | DigiKey | RHM510KCT-ND | http://www.digikey.com/product-detail/en/rohm-semiconductor/ESR10EZPJ511/RHM510KCT-ND/1763033 | Rohm Semiconductor | ESR10EZPJ511 | http://rohmfs.rohm.com/en/products/databook/datasheet/passive/resistor/chip_resistor/esr.pdf | RES SMD 510 OHM 5% 0.4W 0805 | 0.10
U13 | TLP2361 | custom_footprints:TLP2361 |  | Digikey | TLP2361(V4-TPLECT-ND | http://www.digikey.com/product-search/en?keywords=TLP2361(V4-TPLECT-ND | Toshiba Semiconductor and Storage | TLP2361(V4-TPL | E | http://www.semicon.toshiba.co.jp/info/docget.jsp?type=datasheet&lang=en&pid=TLP2361 | OPTOISO 3.75KV PSH PULL SO6-5 | 1.14
C7 | 0.1u | Capacitors_SMD:C_0603_HandSoldering
R9 | 10k | Resistors_SMD:R_0603_HandSoldering
RLY2 | T9AS1D12-5 | custom_footprints:RLY_T9AS1D12-5 |  | Digikey | PB1014-ND | http://www.digikey.com/product-search/en?keywords=PB1014-ND | TE Connectivity Potter & Brumfield Relays | T9AS1D12-5 | http://www.te.com/commerce/DocumentDelivery/DDEController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 | RELAY GEN PURPOSE SPST 30A 5V | 4.22
C28 | .1u | Capacitors_SMD:C_0603_HandSoldering |  | DigiKey | 399-7845-1-ND | http://www.digikey.com/product-detail/en/kemet/C0603C104M5RACTU/399-7845-1-ND/3471568 | Kemet | C0603C104M5RACTU | http://www.kemet.com/docfinder?Partnumber=C0603C104M5RACTU | 0.10µF 50V Ceramic Capacitor X7R 0603 (1608 Metric) 0.063" L x 0.031" W (1.60mm x 0.80mm) | 0.10
C29 | .1u | Capacitors_SMD:C_0603_HandSoldering |  | DigiKey | 490-6112-1-ND | http://www.digikey.com/product-detail/en/murata-electronics-north-america/GRM0335C1H100JA01D/490-6112-1-ND/3845312 | Murata Electronics North America | GRM0335C1H100JA01D | http://www.murata.com/~/media/webrenewal/support/library/catalog/products/capacitor/mlcc/c02e.pdf | 10pF 50V Ceramic Capacitor C0G | NP0 0201 (0603 Metric) 0.024" L x 0.012" W (0.60mm x 0.30mm) | 0.10
R5 | 510 | Resistors_SMD:R_0603_HandSoldering |  | DigiKey | RHM510KCT-ND | http://www.digikey.com/product-detail/en/rohm-semiconductor/ESR10EZPJ511/RHM510KCT-ND/1763033 | Rohm Semiconductor | ESR10EZPJ511 | http://rohmfs.rohm.com/en/products/databook/datasheet/passive/resistor/chip_resistor/esr.pdf | RES SMD 510 OHM 5% 0.4W 0805 | 0.10
U11 | MCP2551-I/SN | Housings_SOIC:SOIC-8_3.9x4.9mm_Pitch1.27mm |  | Digikey | MCP2551-I/SN-ND | http://www.digikey.com/product-search/en?keywords=MCP2551-I%2FSN | Microchip | MCP2551-I/SN | http://ww1.microchip.com/downloads/en/DeviceDoc/21667f.pdf | CAN Interface IC | 1.02 |  |  | http://www.microchip.com/wwwproducts/Devices.aspx?dDocName=en010405
R25 | 120 | Resistors_SMD:R_0805_HandSoldering
R24 | 1k | Resistors_SMD:R_0603_HandSoldering
C19 | 0.1u | Capacitors_SMD:C_0603_HandSoldering
C20 | 0.1u | Capacitors_SMD:C_0603_HandSoldering
U12 | FT232RL | Housings_SSOP:SSOP-28_5.3x10.2mm_Pitch0.65mm |  | Digikey | 768-1007-1-ND | http://www.digikey.com/product-detail/en/FT232RL-REEL/768-1007-1-ND/1836402 | FTDI | FT232RL-REEL | http://www.ftdichip.com/Support/Documents/DataSheets/ICs/DS_FT232R.pdf | IC USB FS SERIAL UART 28-SSOP | 4.50
C21 | 0.1u | Capacitors_SMD:C_0603_HandSoldering
D15 | SK310A-LTP | custom_footprints:do214ac |  | Digikey | SK310A-LTPMSCT-ND | http://www.digikey.com/product-detail/en/SK310A-LTP/SK310A-LTPMSCT-ND/2642066 | Micro Commercial Components (MMC) | SK310A-LTP | http://www.mccsemi.com/up_pdf/SK32A-LT~SK310A-LT%28DO-214AC%29.PDF | Schottky Diodes & Rectifiers DIODE SCHOTTKY 100V 3A DO214AC | 0.57
J1 | USB | custom_footprints:conn_usb_B |  | Digikey | A114945-ND | http://www.digikey.com/product-detail/en/1734346-1/A114945-ND/1891565 | TE Connectivity | 1734346-1 | http://www.te.com/catalog/pn/en/1734346-1?RQPN=1734346-1 | USB Connectors B Blk 4pos R/A SMT | 1.36
P5 | JTAG | custom_footprints:JTAG |  | Digikey | 609-4054-ND | http://www.digikey.com/product-detail/en/20021521-00010T1LF/609-4054-ND/2414951 | FCI | 20021521-00010T1LF | http://portal.fciconnect.com/Comergent//fci/drawing/20021521.pdf | Headers & Wire Housings 10P STRT 4WALL GLDFL | 1.10
P3 | EXT I2C | custom_footprints:MOLEX_HEADER_6POS |  | Digikey | WM1344-ND | http://www.digikey.com/product-search/en?keywords=15-91-2065 | Molex | 15-91-2065 |  | Headers & Wire Housings 2.54 WIRE/BOARD HDR Right Angle 6 CKT | 4.20 |  |  | http://www.molex.com/molex/products/datasheet.jsp?part=active/0015912065_PCB_HEADERS.xml
P4 | GPIO | Connect:IDC_Header_Straight_16pins |  | Digikey | 3M11931-ND | http://www.digikey.com/product-search/en?keywords=30316-6002HB | 3M | 30316-6002HB | http://www.mouser.com/ds/2/1/TS0818-221281.pdf | Headers & Wire Housings 26P STRT 4WALL GLDFL | 0.78
J2 | BACKPLANE CONNECTOR | Connect:DB37FD |  | Digikey | 5237FE-ND | http://www.digikey.com/product-detail/en/171-037-213R011/5237FE-ND/858167 | Norcomp Inc | 171-037-213R011 |  | D-Sub Connector Receptacle Female Sockets 37 Position Through Hole Solder | 3.88
R35 | 100 | Resistors_SMD:R_0603_HandSoldering
R36 | 100 | Resistors_SMD:R_0603_HandSoldering
P2 | CDETECT | custom_footprints:MOLEX_HEADER_2POS |  | Digikey | WM1340-ND | http://www.digikey.com/product-search/en?keywords=15-91-2025 | Molex | 15-91-2025 | http://www.mouser.com/ds/2/276/0015912025_PCB_HEADERS-227317.pdf | Headers 2.54 WIRE/BOARD HDR Right Angle 2 CKT | 2.61
J3 | RJ12 | custom_footprints:MOLEX_RJ11 |  | Digikey | WM3789CT-ND | http://www.digikey.com/product-detail/en/0855135002/WM3789CT-ND/2421677 | Molex LLC | 0855135002 | http://www.molex.com/pdm_docs/sd/855135002_sd.pdf | CONN MOD JACK 6P6C VERT UNSHLD | 1.16
P1 | POWER | custom_footprints:AMPCONN_4POS |  | Digikey | A113982-ND | http://www.digikey.com/product-detail/en/te-connectivity-amp-connectors/556881-4/A113982-ND/294122 | TE Connectivity AMP Connectors | 556881-4 | http://www.te.com/commerce/DocumentDelivery/DDEController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 | CONN RCPT 4POS 11.18MM PCB SLDR | 8.66 |  |  |  | THIS IS THE BOARD HEADER! A MATING PLUG IS ALSO REQ'D!
R12 | 100 | Resistors_SMD:R_0603_HandSoldering
R21 | 100 | Resistors_SMD:R_0603_HandSoldering
P6 | LDETECT | custom_footprints:MOLEX_HEADER_2POS |  | Digikey | WM1340-ND | http://www.digikey.com/product-search/en?keywords=15-91-2025 | Molex | 15-91-2025 | http://www.mouser.com/ds/2/276/0015912025_PCB_HEADERS-227317.pdf | Headers 2.54 WIRE/BOARD HDR Right Angle 2 CKT | 2.61
C30 | 10u | Capacitors_SMD:C_0805_HandSoldering |  | DigiKey | 478-5266-1-ND | http://www.digikey.com/product-detail/en/avx-corporation/02016D104KAT2A/478-5266-1-ND/1950933 | AVX Corporation | 02016D104KAT2A | http://datasheets.avx.com/cx5r.pdf | 0.10µF 6.3V Ceramic Capacitor X5R 0201 (0603 Metric) 0.024" L x 0.012" W (0.60mm x 0.30mm) | 0.10
R15 | 510 | Resistors_SMD:R_0805_HandSoldering |  | DigiKey | RMCF0805JT510RCT-ND | http://www.digikey.com/product-detail/en/stackpole-electronics-inc/RMCF0805JT510R/RMCF0805JT510RCT-ND/1942552 | Stackpole Electronics Inc. | RMCF0805JT510R | https://www.seielect.com/Catalog/SEI-RMCF_RMCP.pdf | RES SMD 510 OHM 5% 1/8W 0805 | 0.10
U14 | TCA9617B | custom_footprints:TCA9617B | http://www.ti.com/lit/ds/symlink/tca9617b.pdf | Digikey | 296-40579-1-ND | http://www.digikey.com/product-detail/en/texas-instruments/TCA9617BDGKR/296-40579-1-ND/5178456 | TI | TCA9617BDGKR |  | Voltage Level Translator Bidirectional 1 Circuit 2 Channel 8-VSSOP | 1.01
C34 | .1u | Capacitors_SMD:C_0603_HandSoldering |  | DigiKey | 478-5266-1-ND | http://www.digikey.com/product-detail/en/avx-corporation/02016D104KAT2A/478-5266-1-ND/1950933 | AVX Corporation | 02016D104KAT2A | http://datasheets.avx.com/cx5r.pdf | 0.10µF 6.3V Ceramic Capacitor X5R 0201 (0603 Metric) 0.024" L x 0.012" W (0.60mm x 0.30mm) | 0.10
C32 | 10u | Capacitors_SMD:C_0805_HandSoldering |  | DigiKey | 478-5266-1-ND | http://www.digikey.com/product-detail/en/avx-corporation/02016D104KAT2A/478-5266-1-ND/1950933 | AVX Corporation | 02016D104KAT2A | http://datasheets.avx.com/cx5r.pdf | 0.10µF 6.3V Ceramic Capacitor X5R 0201 (0603 Metric) 0.024" L x 0.012" W (0.60mm x 0.30mm) | 0.10
C33 | 10u | Capacitors_SMD:C_0805_HandSoldering |  | DigiKey | 478-5266-1-ND | http://www.digikey.com/product-detail/en/avx-corporation/02016D104KAT2A/478-5266-1-ND/1950933 | AVX Corporation | 02016D104KAT2A | http://datasheets.avx.com/cx5r.pdf | 0.10µF 6.3V Ceramic Capacitor X5R 0201 (0603 Metric) 0.024" L x 0.012" W (0.60mm x 0.30mm) | 0.10
C36 | 10u | Capacitors_SMD:C_0805_HandSoldering |  | DigiKey | 478-5266-1-ND | http://www.digikey.com/product-detail/en/avx-corporation/02016D104KAT2A/478-5266-1-ND/1950933 | AVX Corporation | 02016D104KAT2A | http://datasheets.avx.com/cx5r.pdf | 0.10µF 6.3V Ceramic Capacitor X5R 0201 (0603 Metric) 0.024" L x 0.012" W (0.60mm x 0.30mm) | 0.10
C35 | 10u | Capacitors_SMD:C_0805_HandSoldering |  | DigiKey | 478-5266-1-ND | http://www.digikey.com/product-detail/en/avx-corporation/02016D104KAT2A/478-5266-1-ND/1950933 | AVX Corporation | 02016D104KAT2A | http://datasheets.avx.com/cx5r.pdf | 0.10µF 6.3V Ceramic Capacitor X5R 0201 (0603 Metric) 0.024" L x 0.012" W (0.60mm x 0.30mm) | 0.10
C31 | 10u | Capacitors_SMD:C_0805_HandSoldering |  | DigiKey | 478-5266-1-ND | http://www.digikey.com/product-detail/en/avx-corporation/02016D104KAT2A/478-5266-1-ND/1950933 | AVX Corporation | 02016D104KAT2A | http://datasheets.avx.com/cx5r.pdf | 0.10µF 6.3V Ceramic Capacitor X5R 0201 (0603 Metric) 0.024" L x 0.012" W (0.60mm x 0.30mm) | 0.10
C37 | .1u | Capacitors_SMD:C_0603_HandSoldering |  | DigiKey | 478-5266-1-ND | http://www.digikey.com/product-detail/en/avx-corporation/02016D104KAT2A/478-5266-1-ND/1950933 | AVX Corporation | 02016D104KAT2A | http://datasheets.avx.com/cx5r.pdf | 0.10µF 6.3V Ceramic Capacitor X5R 0201 (0603 Metric) 0.024" L x 0.012" W (0.60mm x 0.30mm) | 0.10
R16 | 510 | Resistors_SMD:R_0805_HandSoldering |  | DigiKey | RMCF0805JT510RCT-ND | http://www.digikey.com/product-detail/en/stackpole-electronics-inc/RMCF0805JT510R/RMCF0805JT510RCT-ND/1942552 | Stackpole Electronics Inc. | RMCF0805JT510R | https://www.seielect.com/Catalog/SEI-RMCF_RMCP.pdf | RES SMD 510 OHM 5% 1/8W 0805 | 0.10
R18 | 510 | Resistors_SMD:R_0805_HandSoldering |  | DigiKey | RMCF0805JT510RCT-ND | http://www.digikey.com/product-detail/en/stackpole-electronics-inc/RMCF0805JT510R/RMCF0805JT510RCT-ND/1942552 | Stackpole Electronics Inc. | RMCF0805JT510R | https://www.seielect.com/Catalog/SEI-RMCF_RMCP.pdf | RES SMD 510 OHM 5% 1/8W 0805 | 0.10
R17 | 510 | Resistors_SMD:R_0805_HandSoldering |  | DigiKey | RMCF0805JT510RCT-ND | http://www.digikey.com/product-detail/en/stackpole-electronics-inc/RMCF0805JT510R/RMCF0805JT510RCT-ND/1942552 | Stackpole Electronics Inc. | RMCF0805JT510R | https://www.seielect.com/Catalog/SEI-RMCF_RMCP.pdf | RES SMD 510 OHM 5% 1/8W 0805 | 0.10
R22 | 510 | Resistors_SMD:R_0805_HandSoldering |  | DigiKey | RMCF0805JT510RCT-ND | http://www.digikey.com/product-detail/en/stackpole-electronics-inc/RMCF0805JT510R/RMCF0805JT510RCT-ND/1942552 | Stackpole Electronics Inc. | RMCF0805JT510R | https://www.seielect.com/Catalog/SEI-RMCF_RMCP.pdf | RES SMD 510 OHM 5% 1/8W 0805 | 0.10
R26 | 510 | Resistors_SMD:R_0805_HandSoldering |  | DigiKey | RMCF0805JT510RCT-ND | http://www.digikey.com/product-detail/en/stackpole-electronics-inc/RMCF0805JT510R/RMCF0805JT510RCT-ND/1942552 | Stackpole Electronics Inc. | RMCF0805JT510R | https://www.seielect.com/Catalog/SEI-RMCF_RMCP.pdf | RES SMD 510 OHM 5% 1/8W 0805 | 0.10

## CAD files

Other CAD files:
AMS Software 3_31/firmware/dist/default/production/firmware.production.obj

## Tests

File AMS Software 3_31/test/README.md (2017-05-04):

#AMS Verification Unit

##Overivew
This software is designed to run on an Arduino Board inside of the AMS Verifcation Unit. The purpose of this software is to automate the verification and configuration process for the AMS boards.

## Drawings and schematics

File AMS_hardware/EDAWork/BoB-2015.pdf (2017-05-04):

4 | 3 | 2 | 1

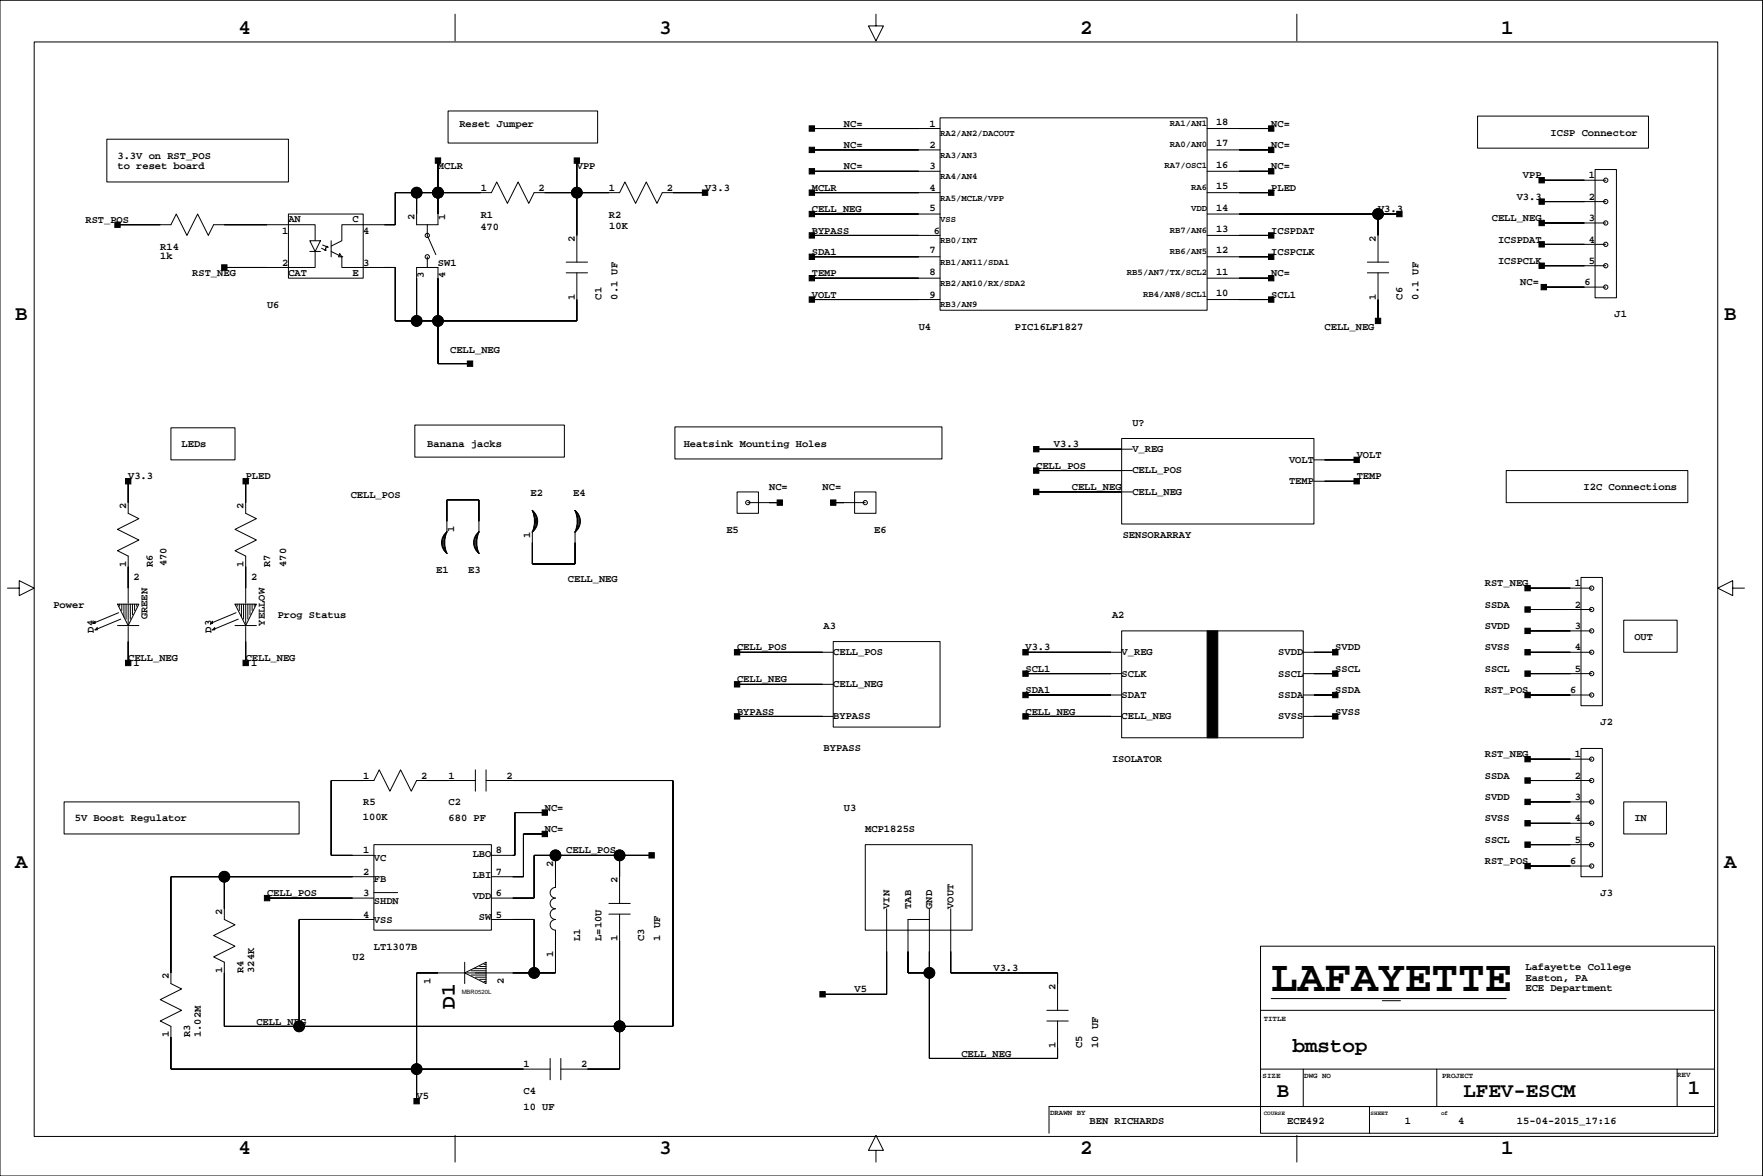
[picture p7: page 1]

R9
470

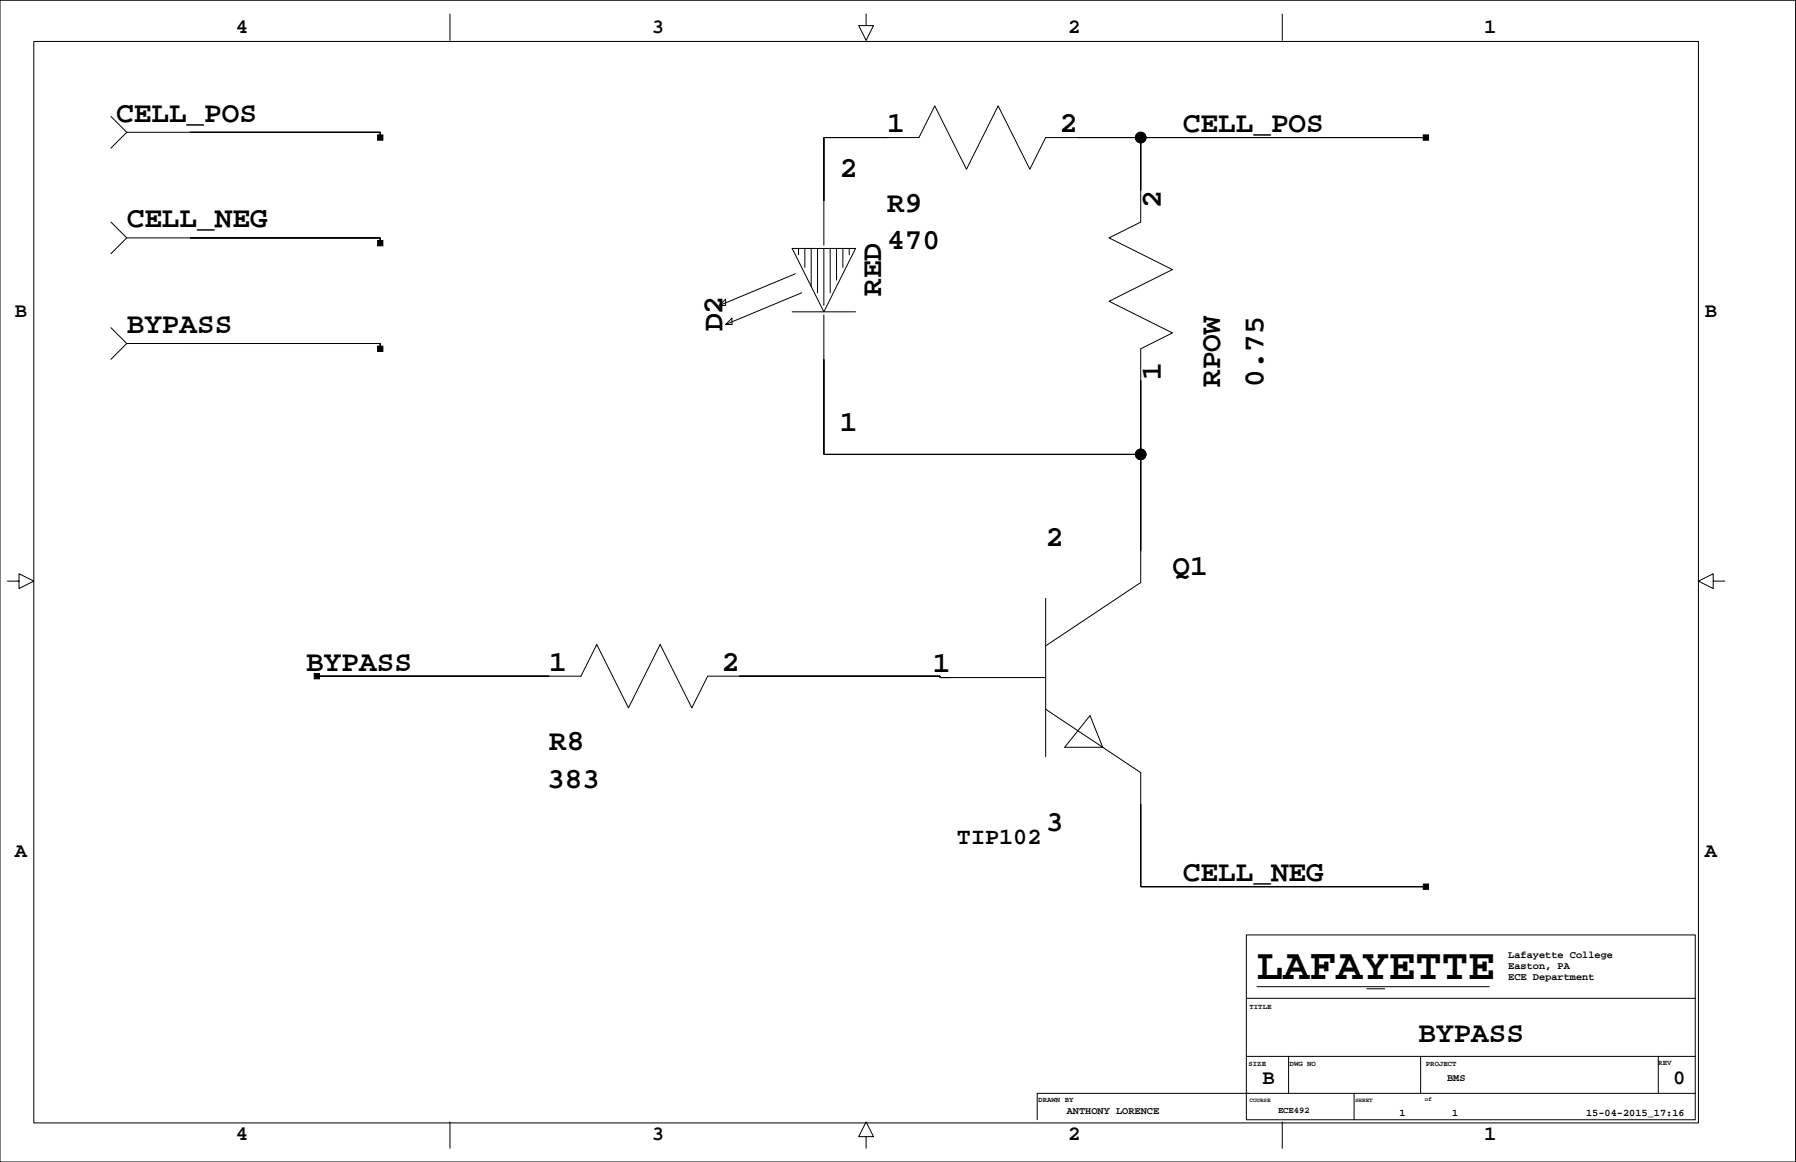
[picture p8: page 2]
BYPASS; ANTHONY LORENCE; BMS; ECE492; ECE Department; Easton, PA; Lafayette College; TITLE; LAFAYETTE; RED; RPOW; TIP102; CELL_POS; CELL_NEG

# SDAT

# SCLK

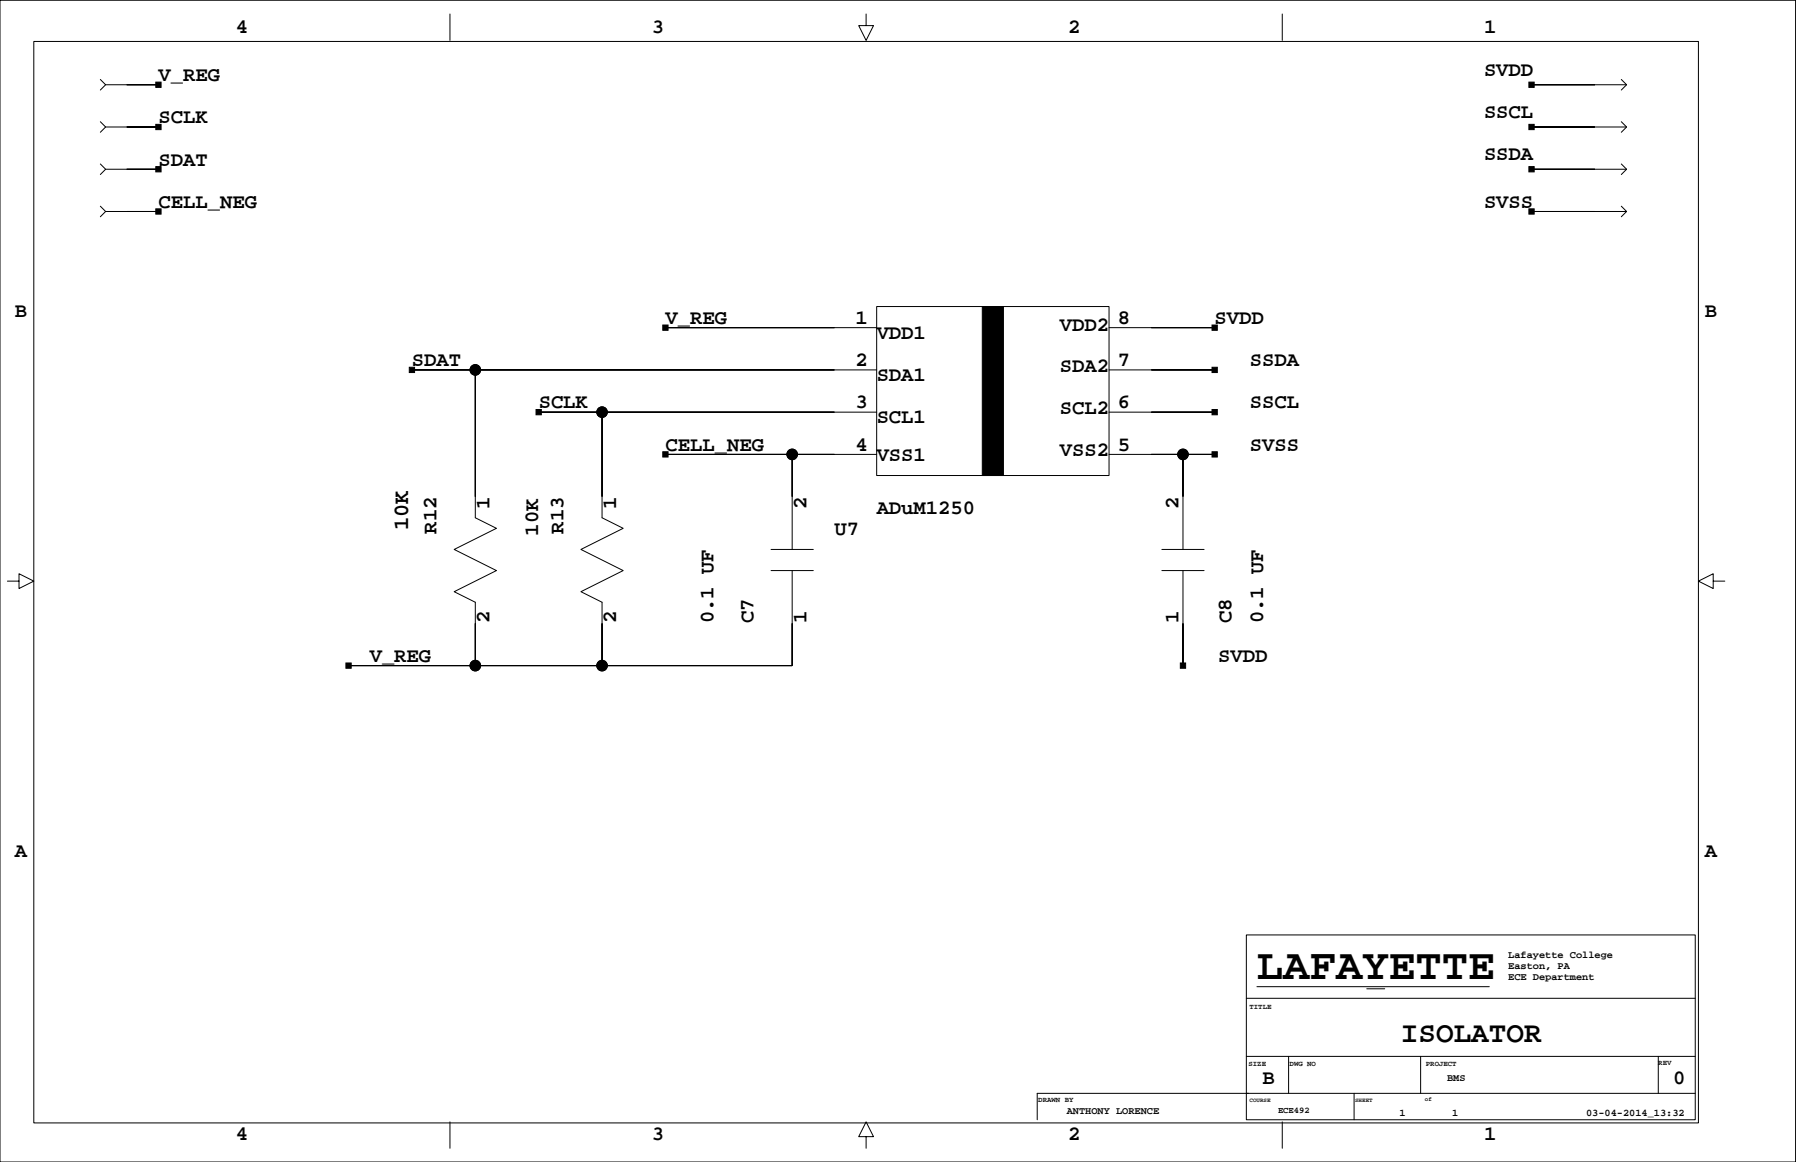
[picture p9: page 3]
ISOLATOR; ECE Department; Easton, PA; Lafayette College; TITLE; LAFAYETTE; VDD1; VSS1; SCL1; SDA1; VSS2; SCL2; SDA2; VDD2; ADuM1250; SDAT; SCLK; CELL_NEG; SVSS; SVDD; SSDA; SSCL; V_REG

### 1.8V Max

### 1.8V Max

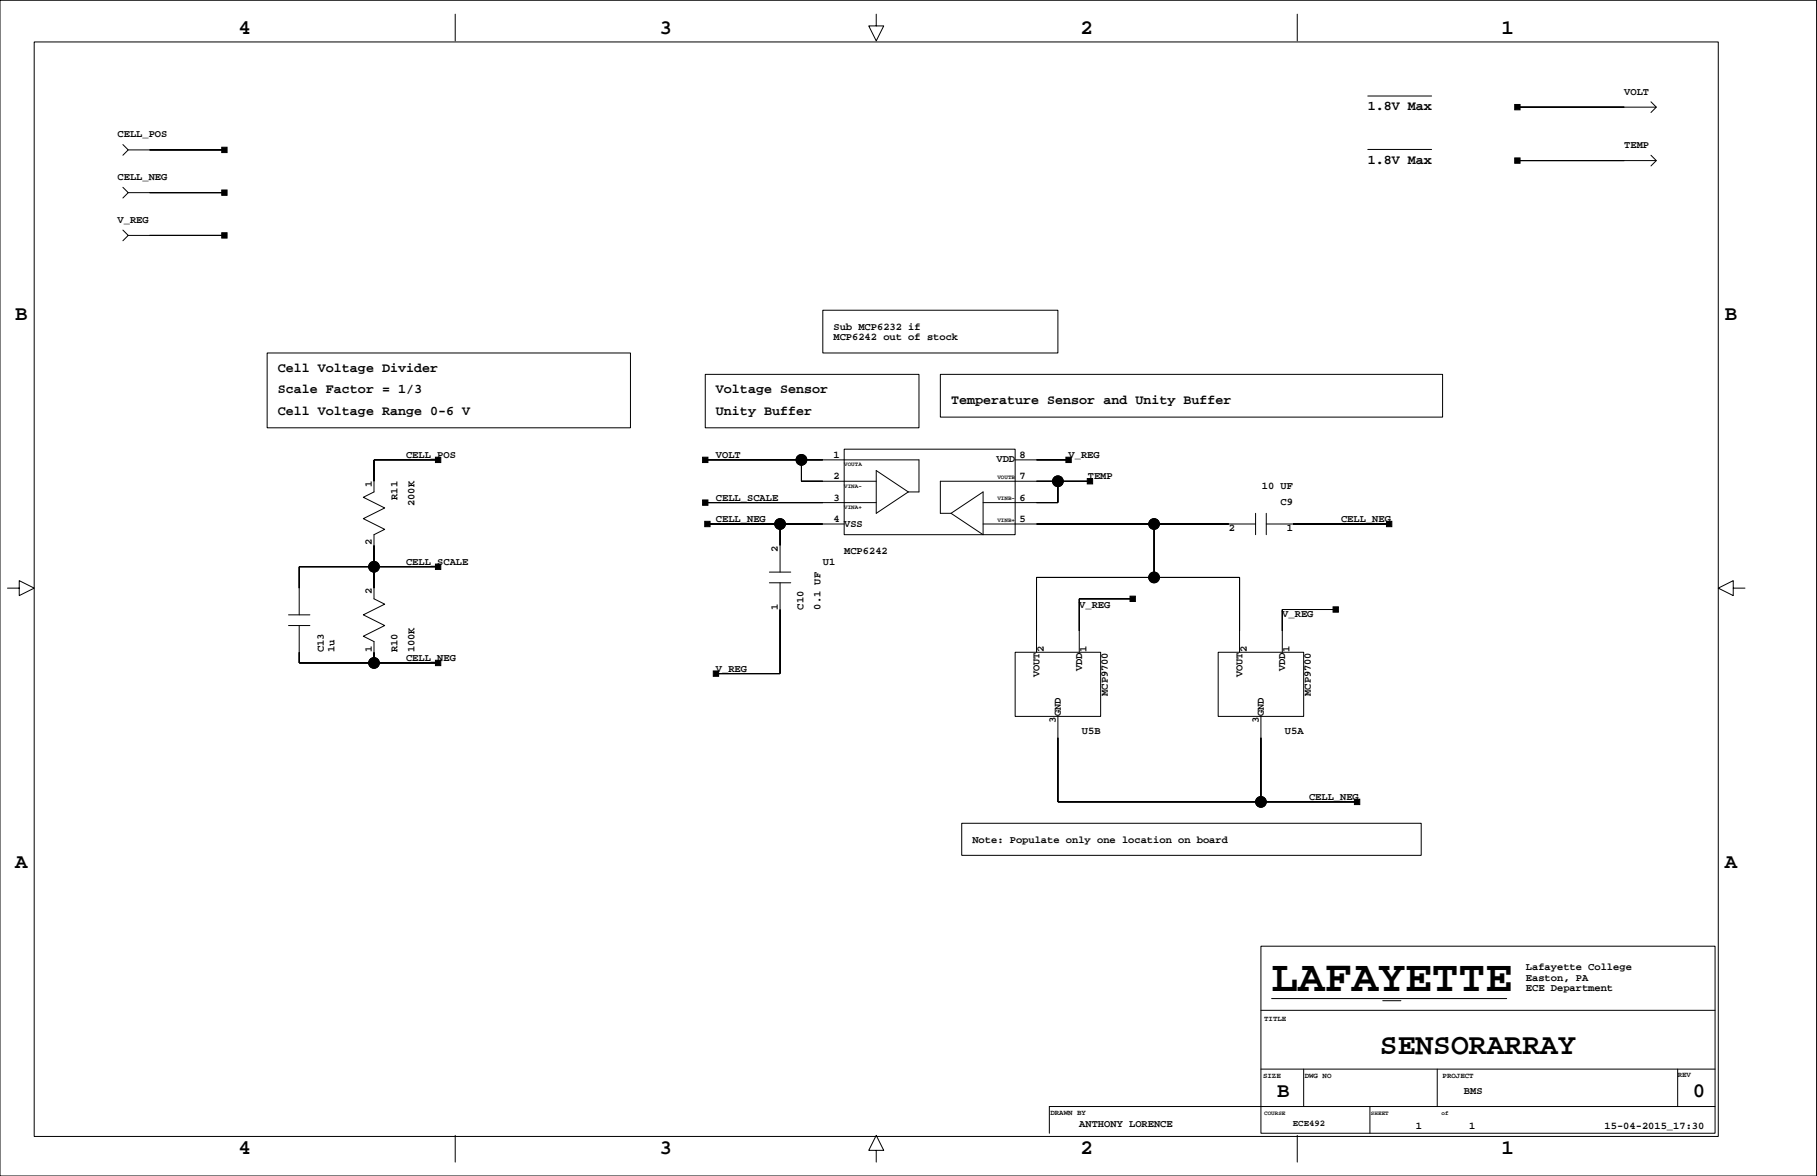
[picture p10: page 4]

Temperature Sensor and Unity Buffer

Note: Populate only one location on board

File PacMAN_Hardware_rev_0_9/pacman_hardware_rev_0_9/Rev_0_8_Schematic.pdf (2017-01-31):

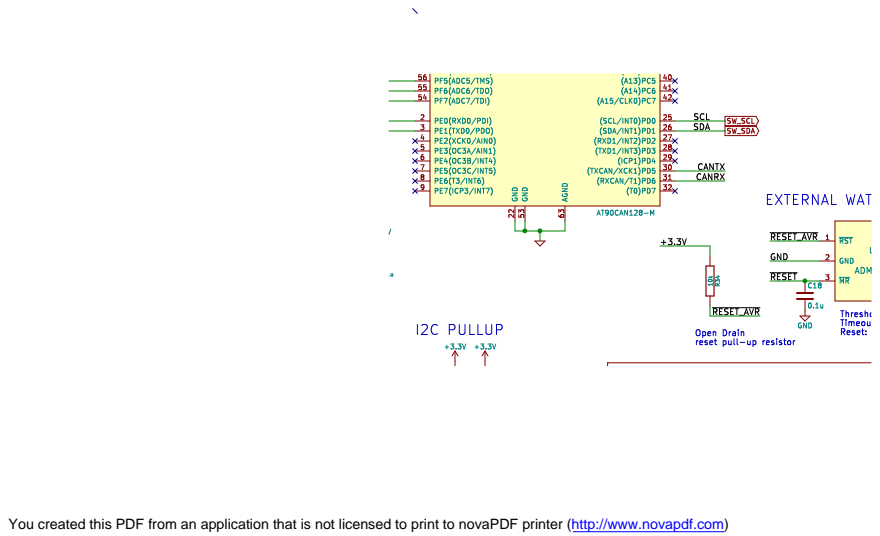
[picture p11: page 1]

You created this PDF from an application that is not licensed to print to novaPDF printer (http://www.novapdf.com)

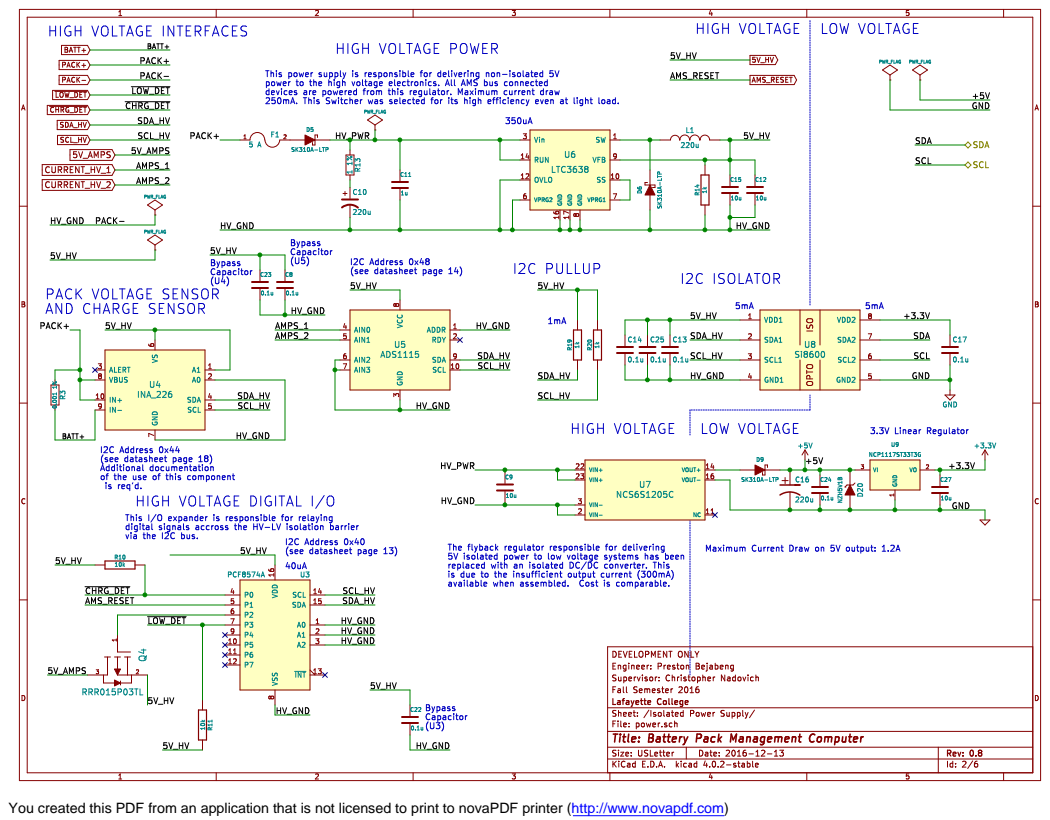
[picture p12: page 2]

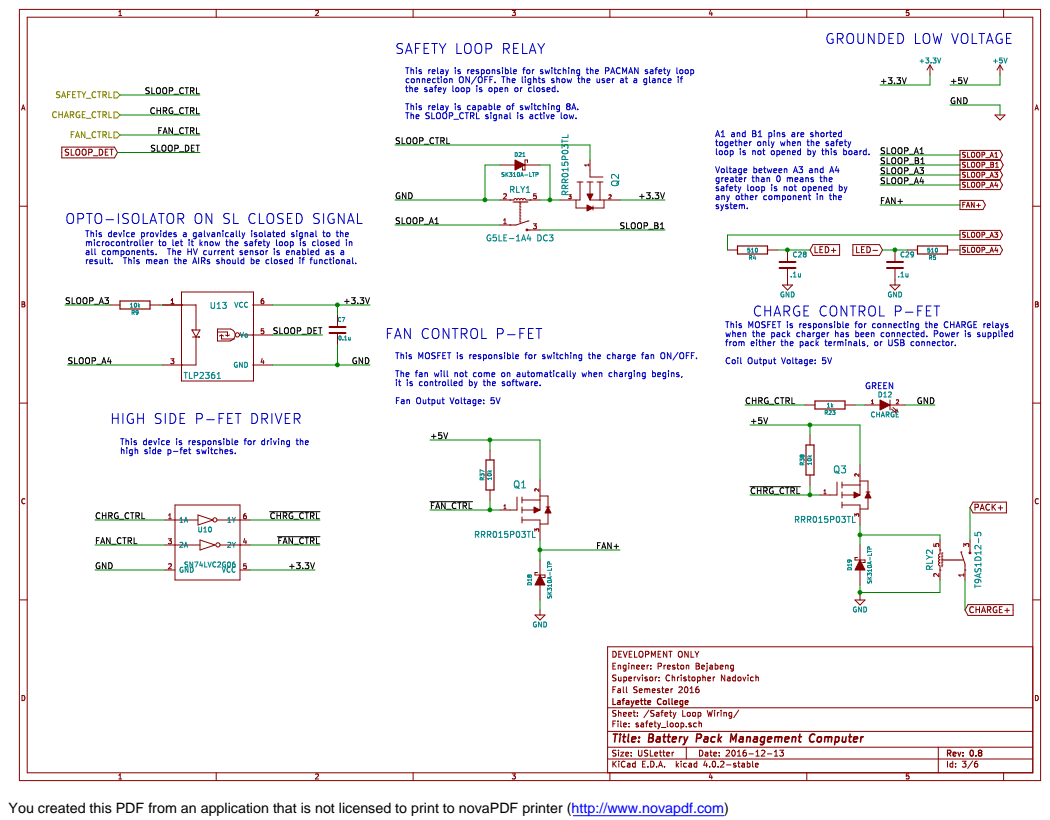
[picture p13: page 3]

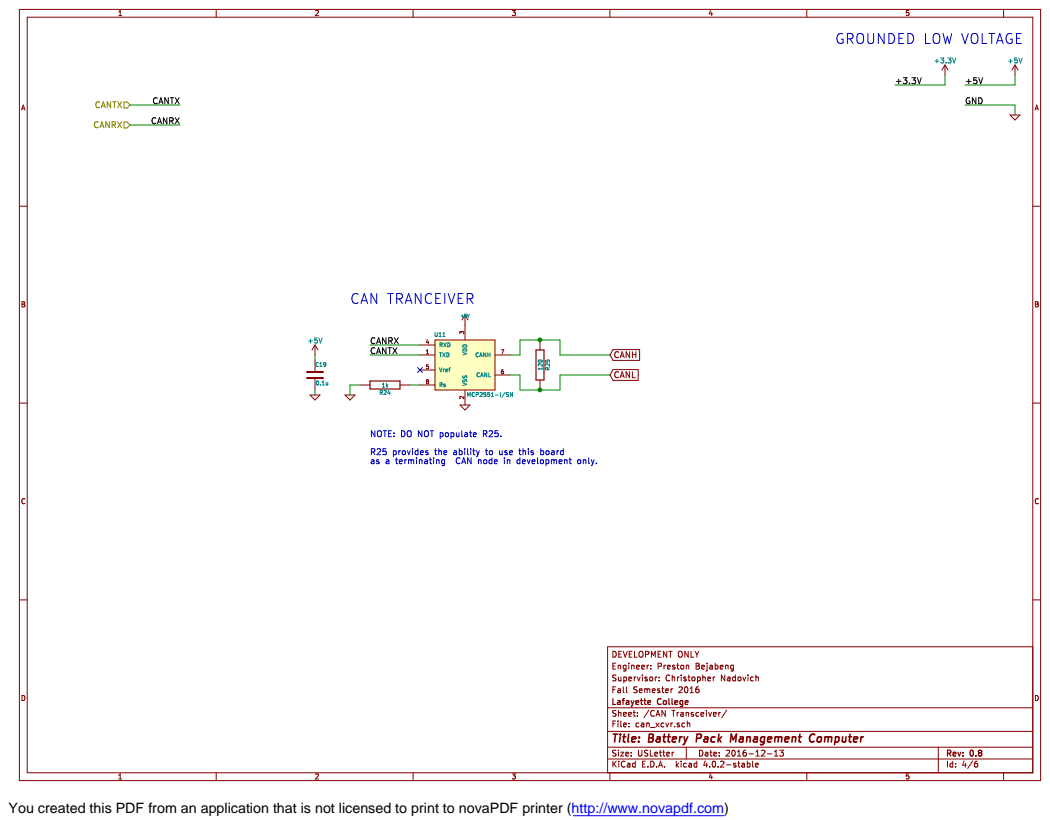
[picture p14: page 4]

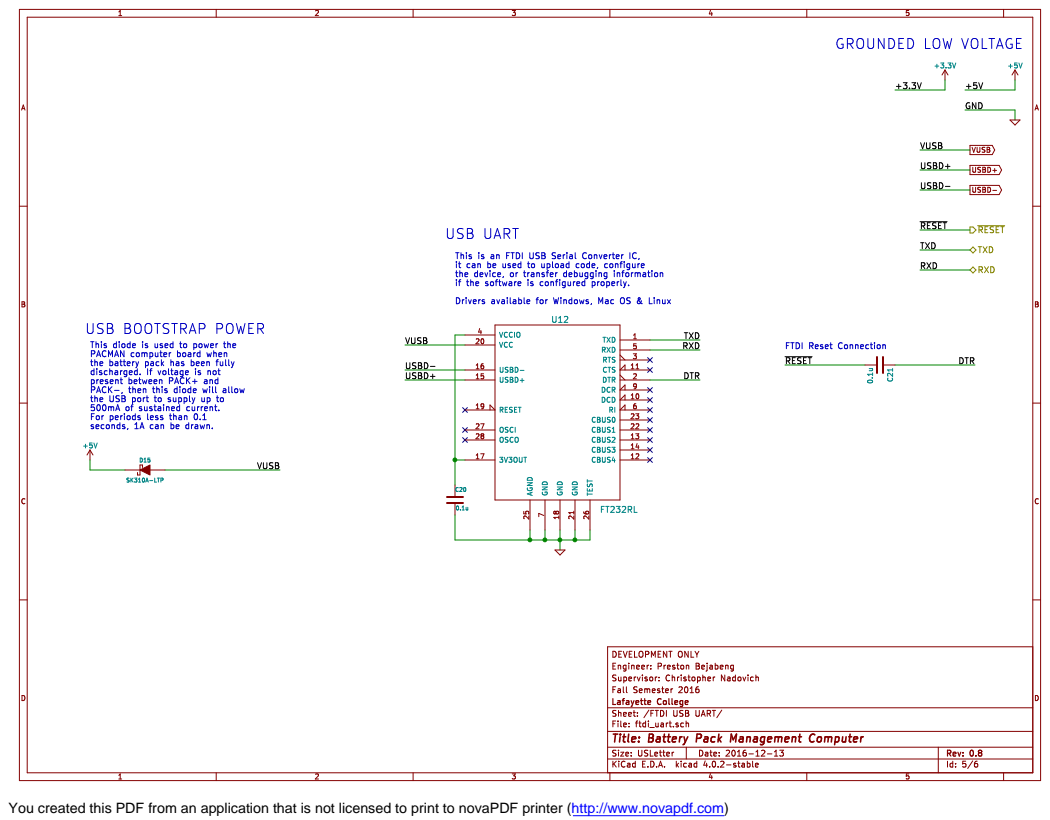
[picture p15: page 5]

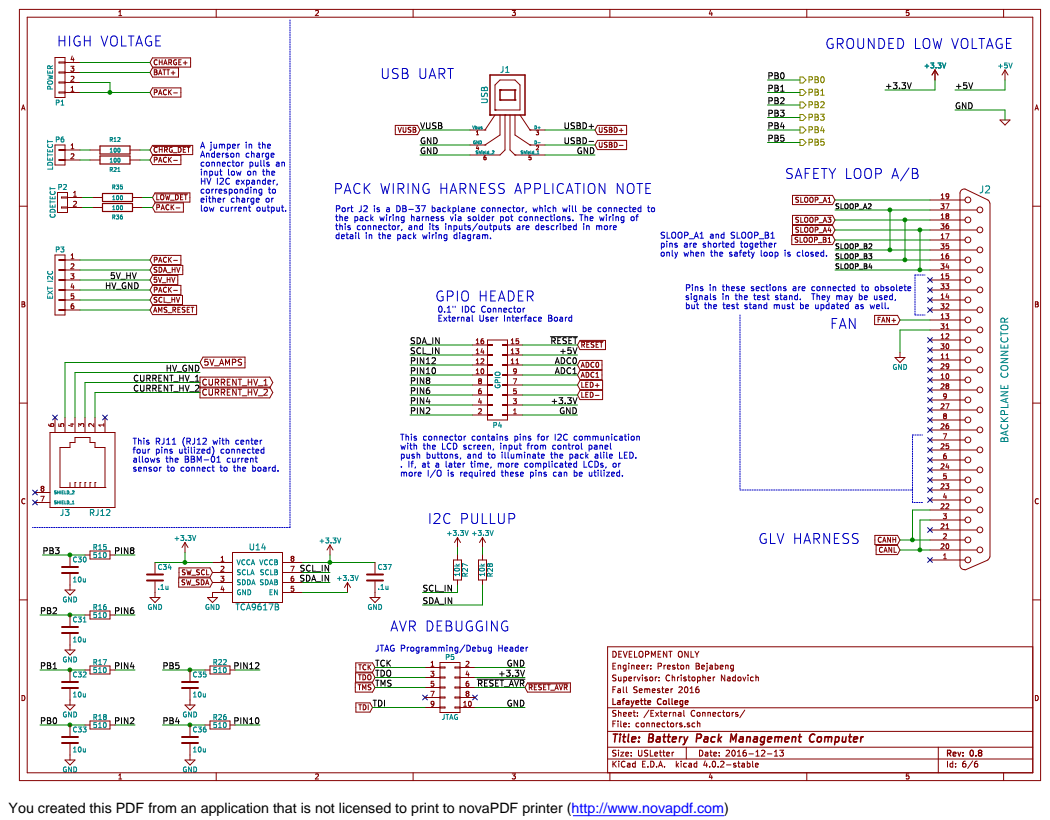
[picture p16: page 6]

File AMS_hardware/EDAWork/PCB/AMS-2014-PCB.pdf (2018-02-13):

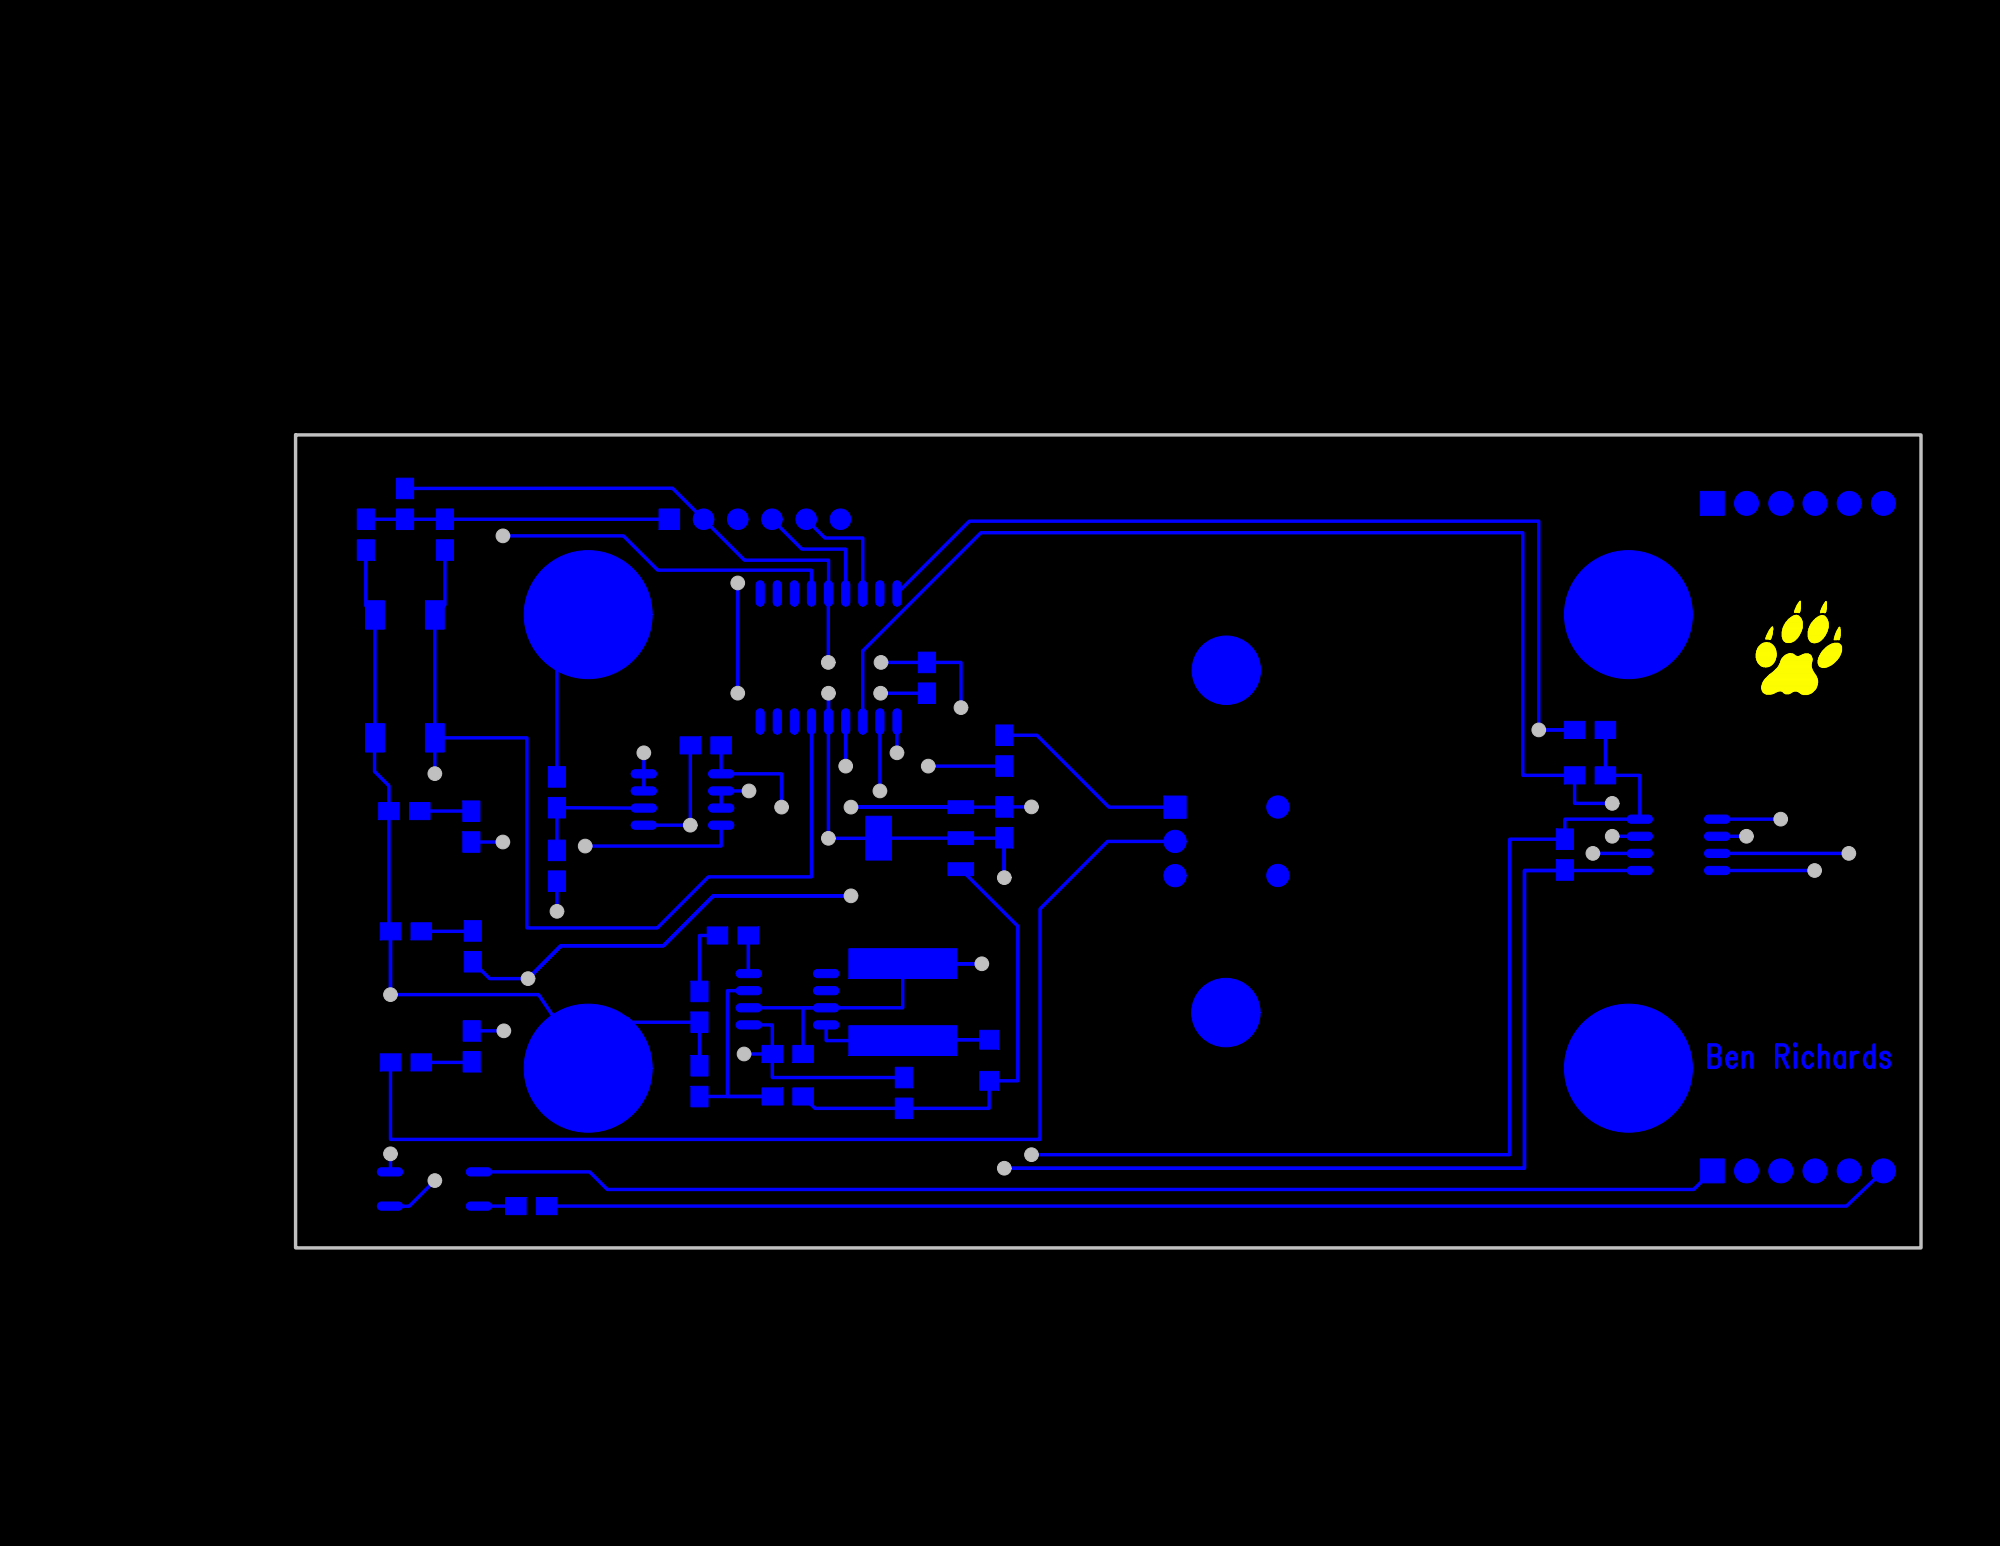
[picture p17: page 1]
Ben Richards; C1C¹x1 C¹x2; C2C²x1 C²x2; C3C³x1; C³x2; C4C⁴x1 C⁴x2; C5C⁵x1 C⁵x2; C10C¹⁰x2; C¹⁰x1; C7C⁷x1 C⁷x2; C6C⁶x1 C⁶x2; D1D¹x1 D¹x2; D2D²x1; D²x2; D3D³x1; D³x2; D4D⁴x1; D⁴x2; E1E¹x1; E2E²x1; E3E³x1; E4E⁴x1; E5E⁵x1; E6E⁶x1; Q1Q¹x1 Q¹x2 Q¹x3; R1R¹x1; R2R²x1; R4 R3R³x2; R³x1 R⁴x1 R⁴x2; R5R⁵x2; R⁵x1; R6R⁶x1 R⁶x2; R7R⁷x1 R⁷x2; R11R¹¹x1 R¹¹x2; R10R¹⁰x1 R¹⁰x2; R13R¹³x1; R¹³x2; R12R¹²x1; R¹²x2 R⁸x1 R⁸x2; R9R⁹x1 R⁹x2; R14R¹⁴x2; R¹⁴x1; RPOWRPOWx1 RPOWx2; SW1SW¹x1 SW¹x2 SW¹x3 SW¹x4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

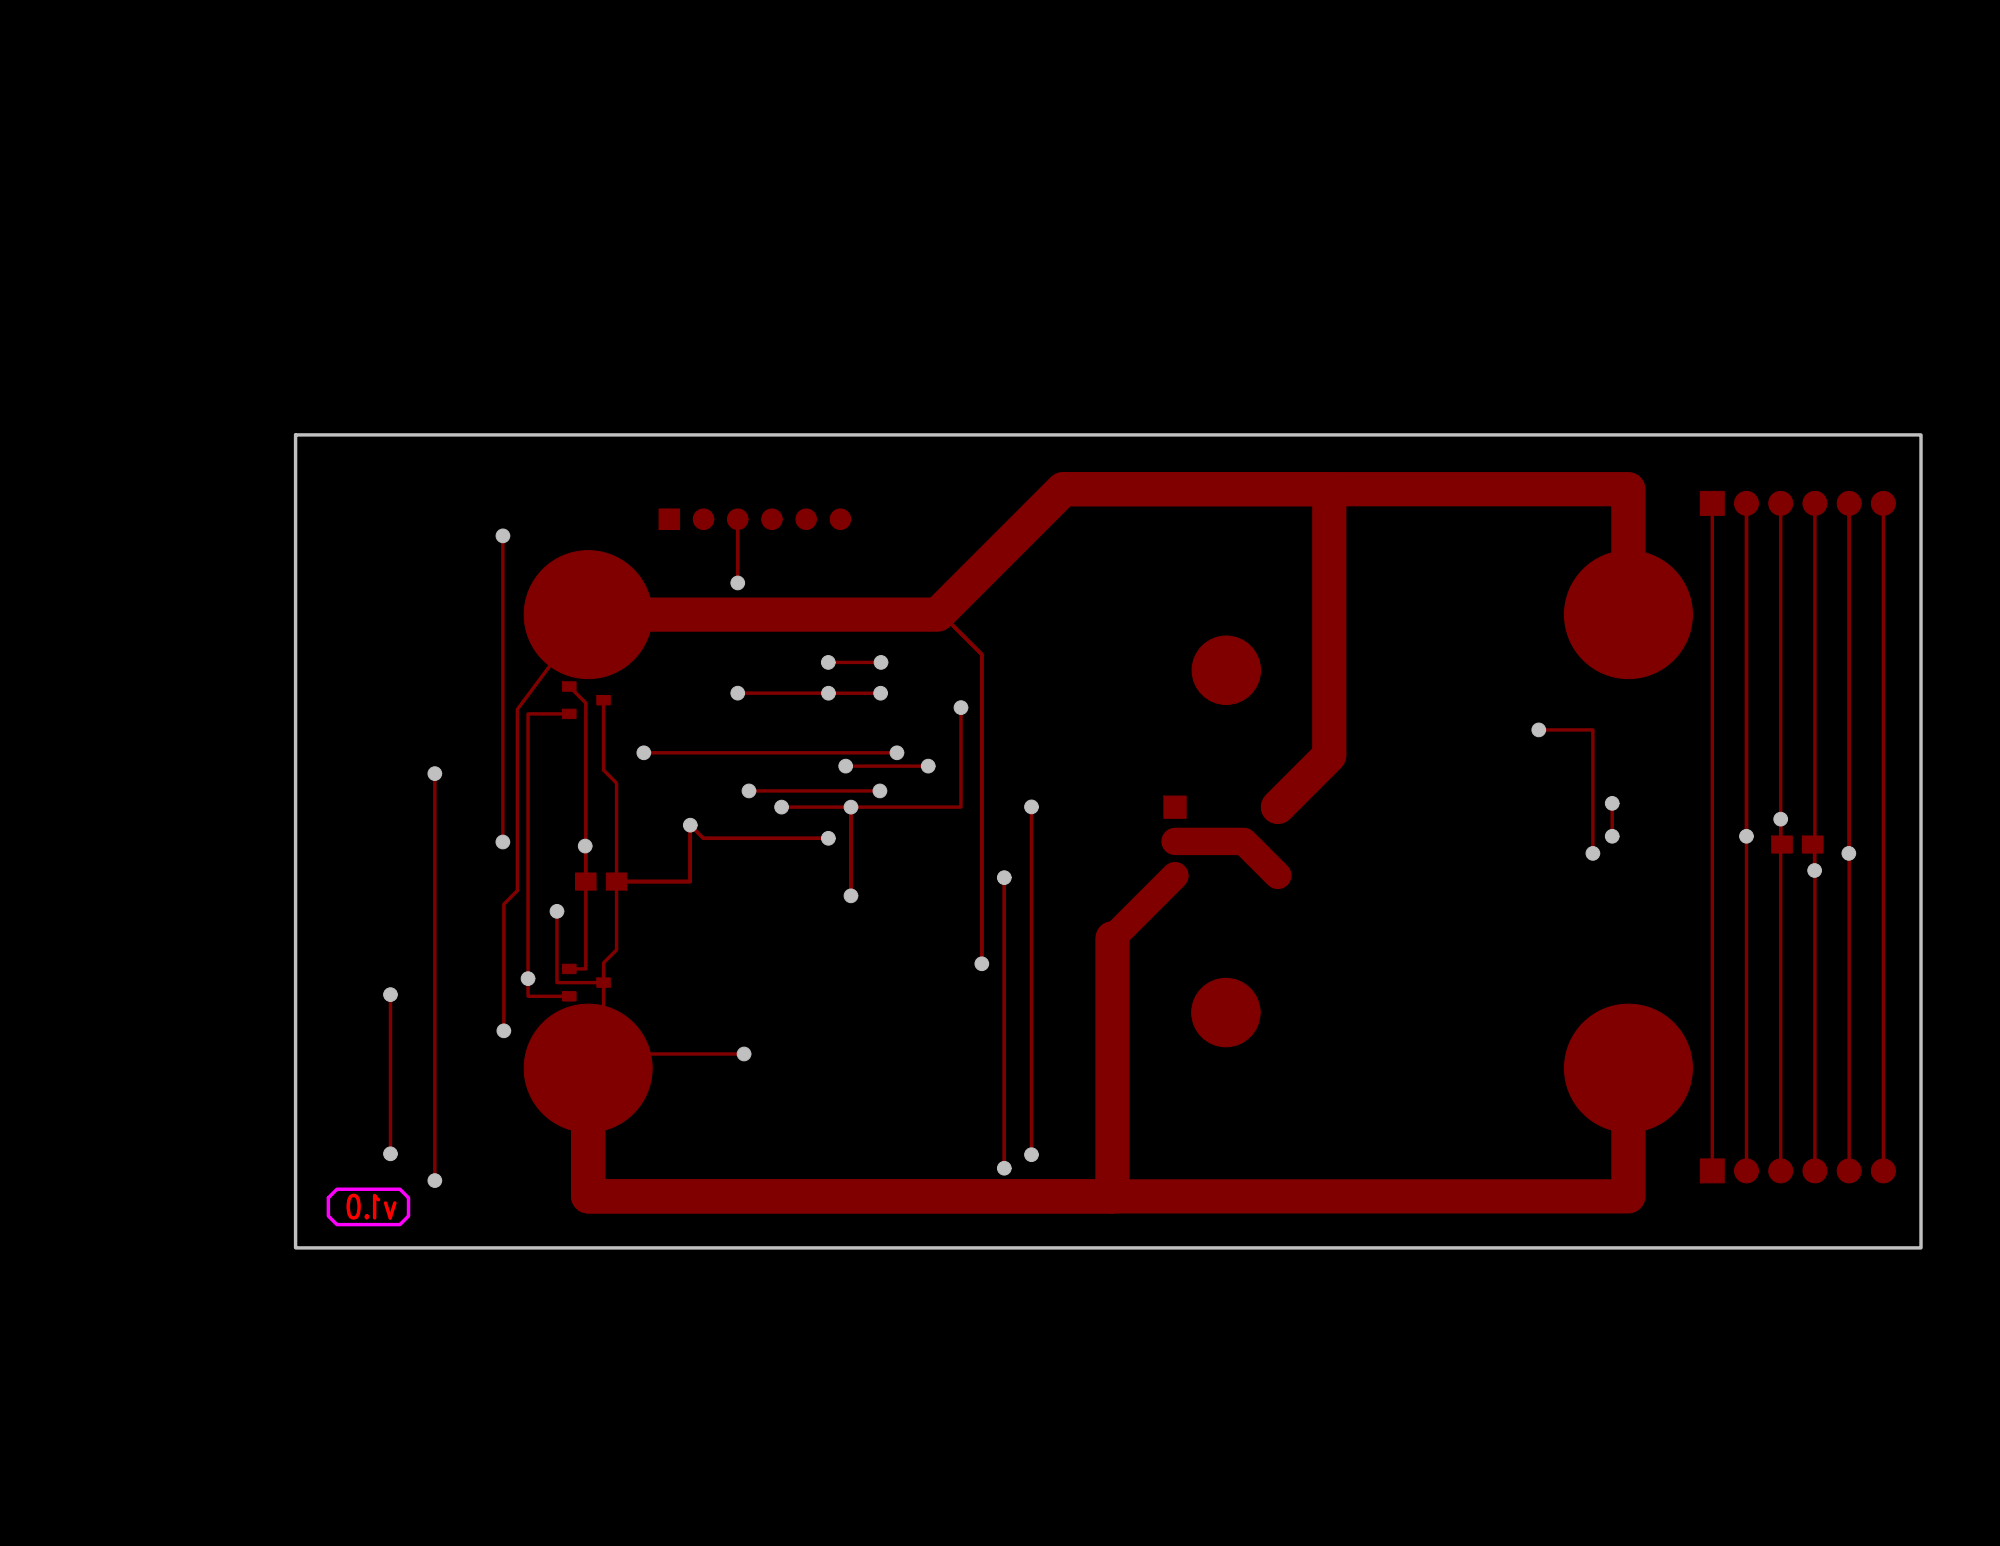
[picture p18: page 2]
C8C⁸x1; C⁸x2; C9C⁹x2; C⁹x1; E1E¹x1; E2E²x1; E3E³x1; E4E⁴x1; E5E⁵x1; E6E⁶x1; Q1x1 Q1x2 Q1x3 RPOWRPOWx1 RPOWx2; U5AU⁵Ax1 U⁵Ax2; U⁵Ax3; U5BU⁵Bx1 U⁵Bx2; U⁵Bx3



# 4750.000mil


RESET PWR ACT BYP

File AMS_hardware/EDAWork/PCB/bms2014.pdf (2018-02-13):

Ben Richards; C1C¹x1 C¹x2; C2C²x1 C²x2; C3C³x1; C³x2; C4C⁴x1 C⁴x2; C5C⁵x1 C⁵x2; C10C¹⁰x2; C¹⁰x1; C7C⁷x1 C⁷x2; C8C⁸x1; C⁸x2; C6C⁶x1 C⁶x2; D1D¹x1 D¹x2; D2D²x1; D²x2; D3D³x1; D³x2; D4D⁴x1; D⁴x2; E1E¹x1; E2E²x1; E3E³x1; E4E⁴x1; E5E⁵x1; E6E⁶x1; Q1Q¹x1 Q¹x2 Q¹x3; R1R¹x1; R2R²x1; R4 R3R³x2; R³x1 R⁴x1 R⁴x2; R5R⁵x2; R⁵x1; R6R⁶x1 R⁶x2; R7R⁷x1 R⁷x2; R11R¹¹x1 R¹¹x2; R10R¹⁰x1 R¹⁰x2; R13R¹³x1; R¹³x2; R12R¹²x1; R¹²x2; R8R⁸x1; R⁸x2; R9R⁹x1 R⁹x2; RPOWRPOWx1 RPOWx2; SW1SW¹x1 SW¹x2 SW¹x3 SW¹x4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

E1E¹x1; E2E²x1; E3E³x1; E4E⁴x1; E5E⁵x1; E6E⁶x1 Q1Q¹x1 Q¹x2 Q¹x3; RPOWRPOWx1 RPOWx2; U5AU⁵Ax1 U⁵Ax2; U⁵Ax3; U5BU⁵Bx1 U⁵Bx2; U⁵Bx3; C9C⁹x2; C⁹x1



# 4750.000mil


ACCUMULATOR MANAGEMENT SYSTEM

RESET PWR ACT BYP

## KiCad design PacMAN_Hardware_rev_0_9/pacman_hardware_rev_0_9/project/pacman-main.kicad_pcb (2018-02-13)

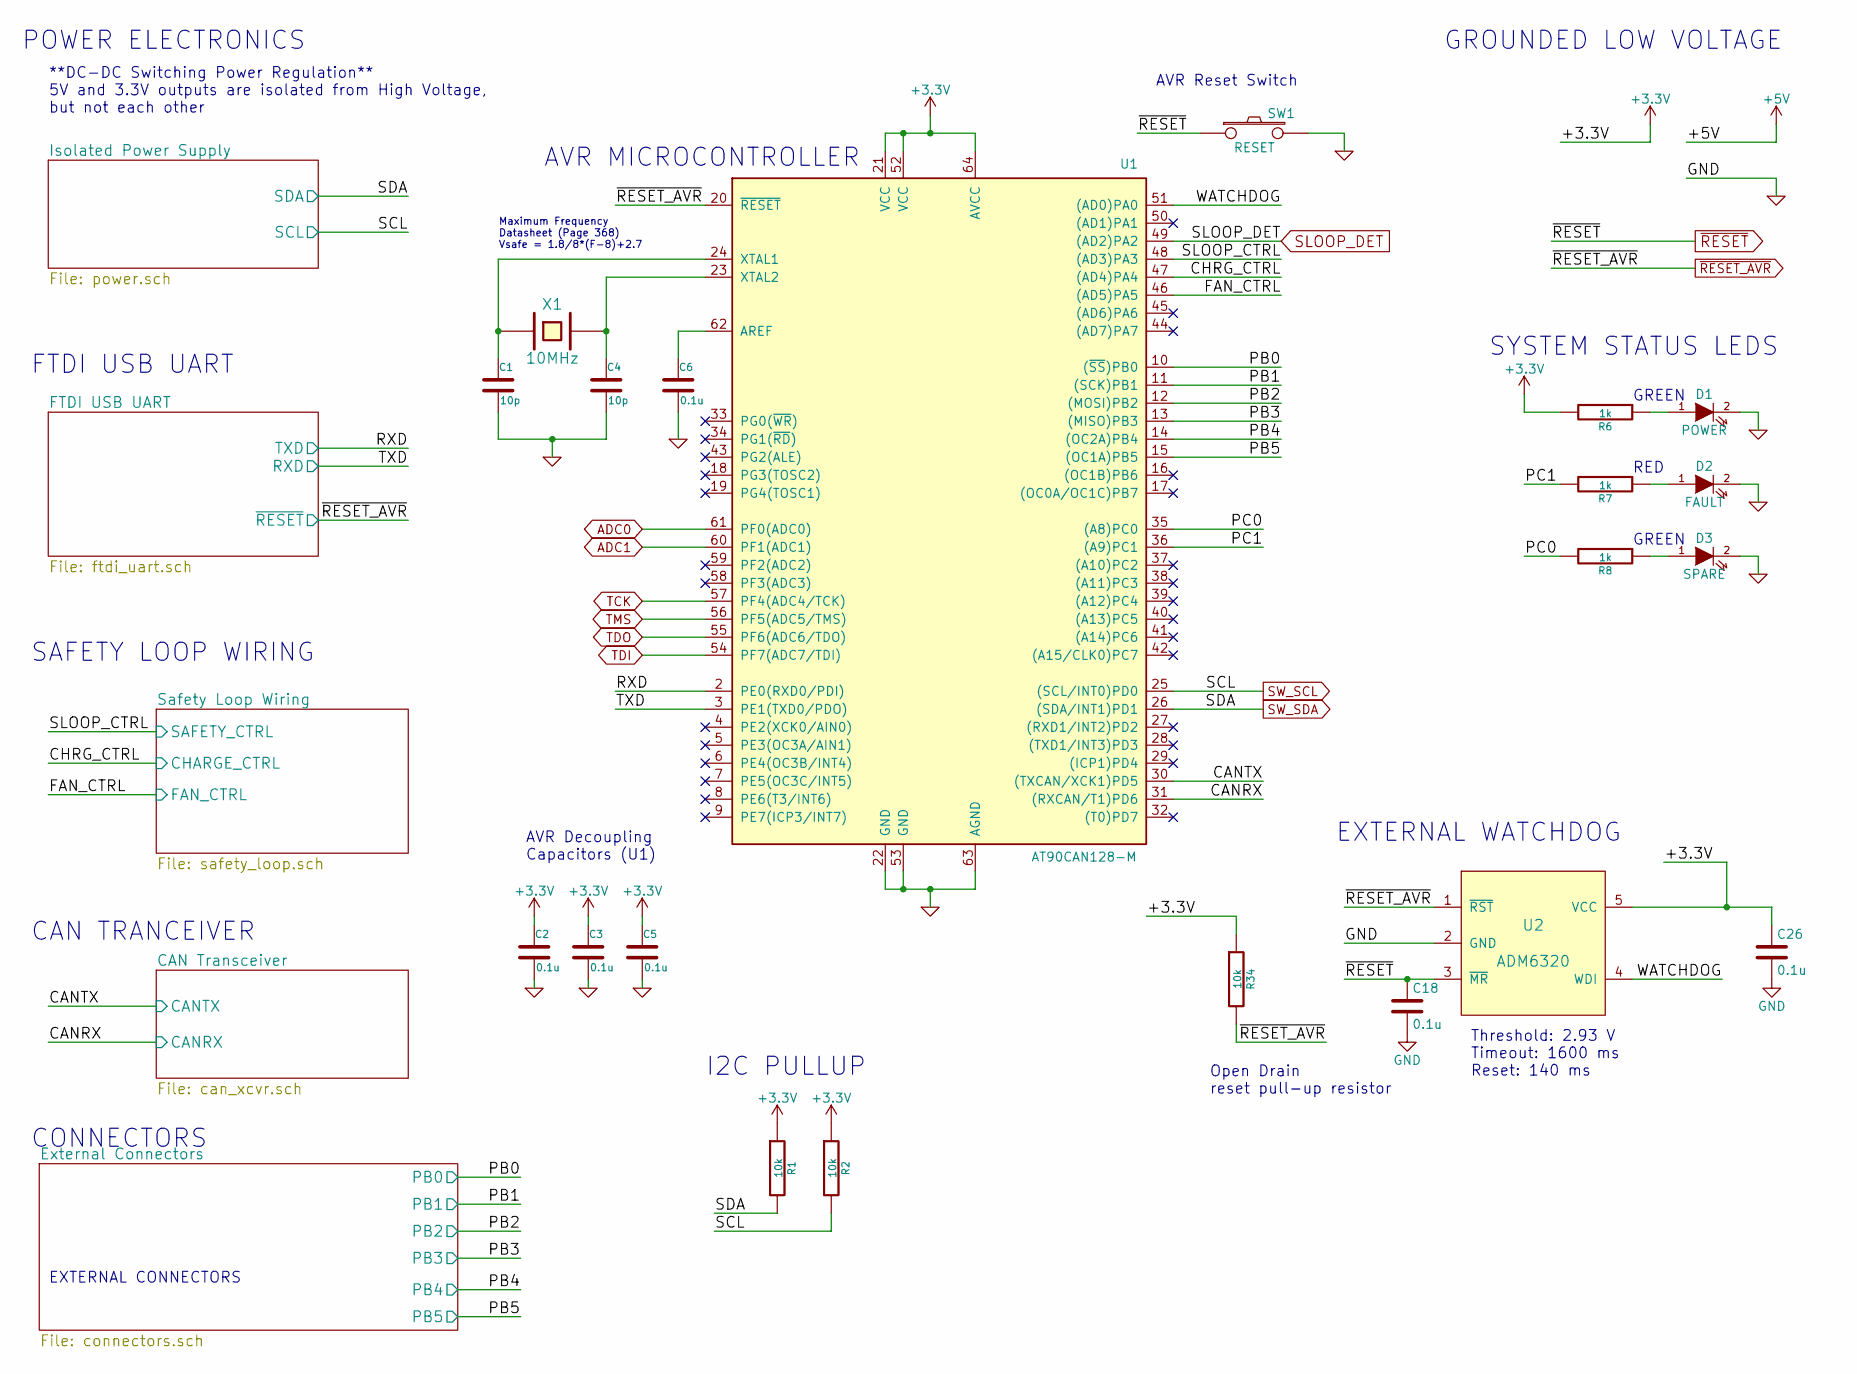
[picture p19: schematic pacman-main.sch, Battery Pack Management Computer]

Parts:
C1, C4: 10p; C_0603_HandSoldering; Manufacturer P/N GRM0335C1H100JA01D
C2, C6: 0.1u; C_0603_HandSoldering
C3, C5: 0.1u; C_0805_HandSoldering
C18, C26: 0.1u; C_0603_HandSoldering; Manufacturer P/N GRM188R71E104KA01D
D1: POWER; LED_0603
D2: FAULT; LED_0603
D3: SPARE; LED_0603
R1, R2, R34: 10k; R_0603_HandSoldering
R6, R7, R8: 1k; R_0603_HandSoldering
SW1: RESET; SW_RACON_8; Manufacturer P/N 1.14100.5030000
U1: AT90CAN128-M; TQFP-64_14x14mm_Pitch0.8mm; Manufacturer P/N AT90CAN128-16AUR
U2: ADM6320; SOT-23-5; Manufacturer P/N ADM6320CY29ARJZ-R7
X1: 10MHz; crystal_TXC_7A; Manufacturer P/N 7A-10.000MAAE-T

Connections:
+3V3: C2.1, C3.1, C5.1, C26.1, R1.1, R2.1, R6.2, R34.1, U1.21 (VCC), U1.52 (VCC), U1.64 (AVCC), U2.5 (VCC); also elsewhere on the board
/CAN Transceiver/CANRX: U1.31 ((RXCAN/T1)PD6); also elsewhere on the board
/CAN Transceiver/CANTX: U1.30 ((TXCAN/XCK1)PD5); also elsewhere on the board
/External Connectors/PB0: U1.10 ((~SS~)PB0); also elsewhere on the board
/External Connectors/PB1: U1.11 ((SCK)PB1); also elsewhere on the board
/External Connectors/PB2: U1.12 ((MOSI)PB2); also elsewhere on the board
/External Connectors/PB3: U1.13 ((MISO)PB3); also elsewhere on the board
/External Connectors/PB4: U1.14 ((OC2A)PB4); also elsewhere on the board
/External Connectors/PB5: U1.15 ((OC1A)PB5); also elsewhere on the board
/FTDI USB UART/RXD: U1.3 (PE1(TXD0/PDO)); also elsewhere on the board
/FTDI USB UART/TXD: U1.2 (PE0(RXD0/PDI)); also elsewhere on the board
/PC0: R8.2, U1.35 ((A8)PC0)
/PC1: R7.2, U1.36 ((A9)PC1)
/Safety Loop Wiring/CHARGE_CTRL: U1.47 ((AD4)PA4); also elsewhere on the board
/Safety Loop Wiring/FAN_CTRL: U1.46 ((AD5)PA5); also elsewhere on the board
/Safety Loop Wiring/SAFETY_CTRL: U1.48 ((AD3)PA3); also elsewhere on the board
/WATCHDOG: U1.51 ((AD0)PA0), U2.4 (WDI)
ADC0: U1.61 (PF0(ADC0)); also elsewhere on the board
ADC1: U1.60 (PF1(ADC1)); also elsewhere on the board
GND: C1.2, C2.2, C3.2, C4.2, C5.2, C6.2, C18.2, C26.2, D1.2 (K), D2.2 (K), D3.2 (K), SW1.2, U1.22 (GND), U1.53 (GND), U1.63 (AGND), U2.2 (GND); also elsewhere on the board
unnamed: C1.1, U1.24 (XTAL1), X1.1
unnamed: C4.1, U1.23 (XTAL2), X1.2
unnamed: C6.1, U1.62 (AREF)
unnamed: D1.1 (A), R6.1
unnamed: D2.1 (A), R7.1
unnamed: D3.1 (A), R8.1
SLOOP_DET: U1.49 ((AD2)PA2); also elsewhere on the board
SW_SCL: R2.2, U1.25 ((SCL/INT0)PD0); also elsewhere on the board
SW_SDA: R1.2, U1.26 ((SDA/INT1)PD1); also elsewhere on the board
TCK: U1.57 (PF4(ADC4/TCK)); also elsewhere on the board
TDI: U1.54 (PF7(ADC7/TDI)); also elsewhere on the board
TDO: U1.55 (PF6(ADC6/TDO)); also elsewhere on the board
TMS: U1.56 (PF5(ADC5/TMS)); also elsewhere on the board
~RESET: C18.1, SW1.1, U2.3 (~MR); also elsewhere on the board
~RESET_AVR: R34.2, U1.20 (~RESET), U2.1 (~RST); also elsewhere on the board

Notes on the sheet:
AVR Reset Switch
AVR Decoupling Capacitors (U1)
AVR MICROCONTROLLER
SYSTEM STATUS LEDS
POWER ELECTRONICS
Maximum Frequency Datasheet (Page 368) Vsafe = 1.8/8*(F-8)+2.7
EXTERNAL WATCHDOG
**DC-DC Switching Power Regulation** 5V and 3.3V outputs are isolated from High Voltage, but not each other
FTDI USB UART
I2C PULLUP
Threshold: 2.93 V Timeout: 1600 ms Reset: 140 ms
EXTERNAL CONNECTORS
GROUNDED LOW VOLTAGE
SAFETY LOOP WIRING
CONNECTORS
CAN TRANCEIVER
Open Drain reset pull-up resistor
GREEN
RED

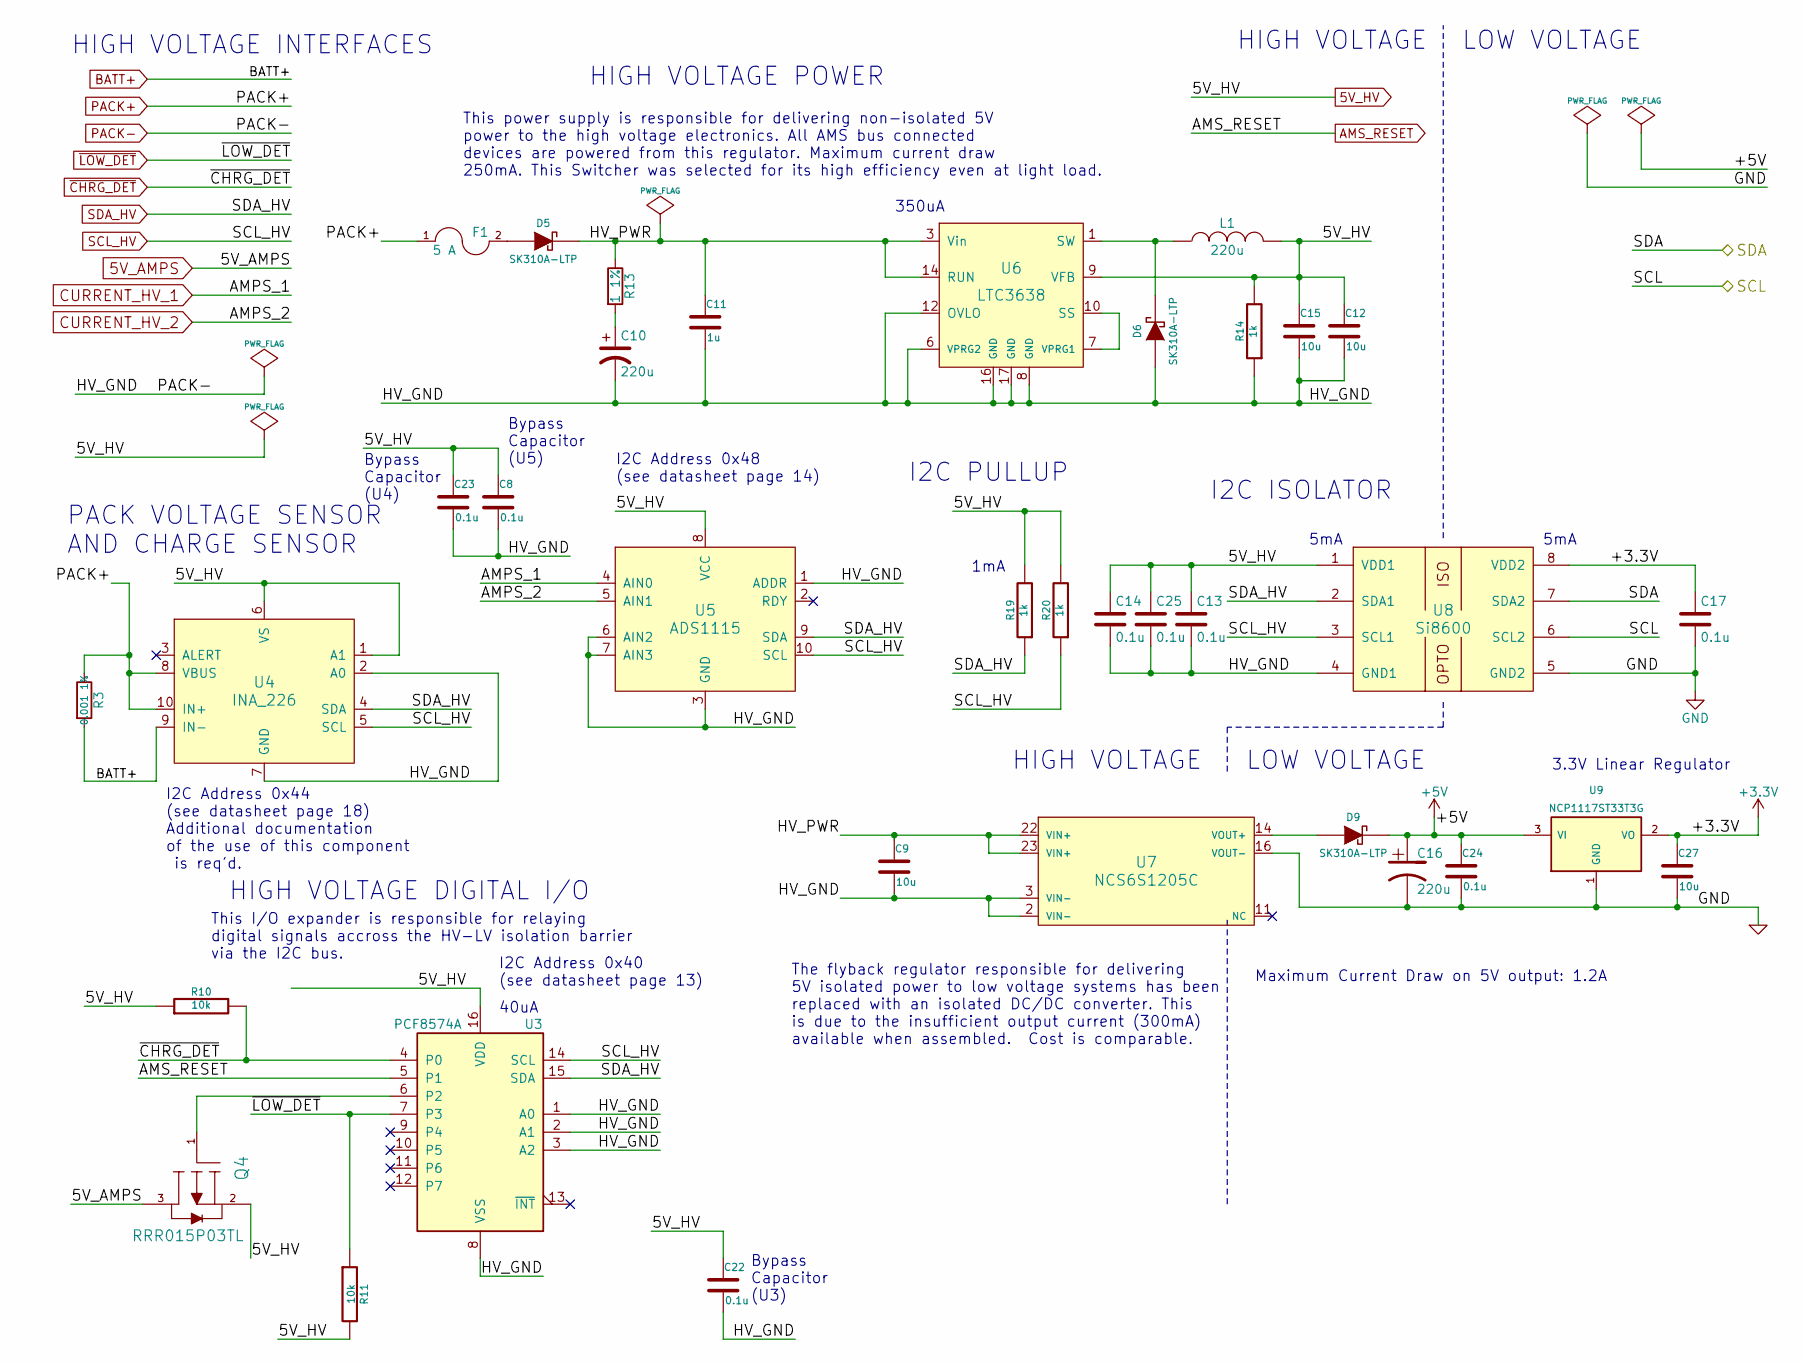
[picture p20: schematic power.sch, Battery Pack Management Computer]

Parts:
C8, C13, C14, C17, C22, C23, C24, C25: 0.1u; C_0603_HandSoldering
C9, C12, C15: 10u; C_1210_HandSoldering; Manufacturer P/N GRM32DF51H106ZA01L
C10: 220u; c_elec_10x10; Manufacturer P/N UCW1H221MNL1GS
C11: 1u; C_0603_HandSoldering; Manufacturer P/N CL10A105KB8NNNC
C16: 220u; c_elec_6.3x7.7; Manufacturer P/N UUR1C221MCL6GS
C27: 10u; C_1210_HandSoldering; Manufacturer P/N CL32A106KAULNNE
D5, D6, D9: SK310A-LTP; do214ac; Manufacturer P/N SK310A-LTP
F1: 5 A; blade_fuse_holder; Manufacturer P/N BK-6010
L1: 220u; SELF-WE-TPC_M; Manufacturer P/N VLS6045EX-221M
Q4: RRR015P03TL; sot346; Manufacturer P/N RRR015P03TL
R3: 0.001 1%; CSNL1206; Manufacturer P/N CSNL1206FT1L00
R10, R11: 10k; R_0603_HandSoldering
R13: 1 1%; R_0805_HandSoldering
R14, R19, R20: 1k; R_0805_HandSoldering
U3: PCF8574A; SOIC-16_7.5x10.3mm_Pitch1.27mm; Manufacturer P/N PCF8574AT3518
U4: INA_226; msop_10_ads1015; Manufacturer P/N INA226AIDGSR
U5: ADS1115; msop_10_ads1015; Manufacturer P/N ADS1115IDGSR
U6: LTC3638; TSSOP16_LTC3638; Manufacturer P/N LTC3638EMSE#PBF
U7: NCS6S1205C; Manufacturer P/N NCS6S1205C
U8: Si8600; SOIC-8_3.9x4.9mm_Pitch1.27mm; Manufacturer P/N Si8600AC-B-IS
U9: NCP1117ST33T3G; SOT-223; Manufacturer P/N NCP1117ST33T3G

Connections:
5V_AMPS: Q4.3 (S); also elsewhere on the board
5V_HV: C8.1, C12.1, C13.1, C14.1, C15.1, C22.1, C23.1, C25.1, L1.2, Q4.2 (D), R10.1, R11.2, R14.2, R19.2, R20.2, U3.16 (VDD), U4.1 (A1), U4.6 (VS), U5.8 (VCC), U6.9 (VFB), U8.1 (VDD1); also elsewhere on the board
+3V3: C17.1, C27.1, U8.8 (VDD2), U9.2 (VO); also elsewhere on the board
+5V: C16.1, C24.1, D9.2 (K), U9.3 (VI); also elsewhere on the board
/Isolated Power Supply/HV_PWR: C9.1, C11.1, D5.2 (K), R13.1, U6.3 (Vin), U6.14 (RUN), U7.22 (VIN+), U7.23 (VIN+)
AMS_RESET: U3.5 (P1); also elsewhere on the board
BATT+: R3.2, U4.9 (IN-); also elsewhere on the board
CURRENT_HV_1: U5.4 (AIN0); also elsewhere on the board
CURRENT_HV_2: U5.5 (AIN1); also elsewhere on the board
GND: C16.2, C17.2, C24.2, C27.2, U7.16 (VOUT-), U8.5 (GND2), U9.1 (GND); also elsewhere on the board
unnamed: C10.1, R13.2
unnamed: D5.1 (A), F1.2
unnamed: D6.2 (K), L1.1, U6.1 (SW)
unnamed: D9.1 (A), U7.14 (VOUT+)
unnamed: Q4.1 (G), U3.6 (P2)
unnamed: U6.7 (VPRG1), U6.10 (SS)
PACK+: F1.1, R3.1, U4.8 (VBUS), U4.10 (IN+); also elsewhere on the board
PACK-: C8.2, C9.2, C10.2, C11.2, C12.2, C13.2, C14.2, C15.2, C22.2, C23.2, C25.2, D6.1 (A), R14.1, U3.1 (A0), U3.2 (A1), U3.3 (A2), U3.8 (VSS), U4.2 (A0), U4.7 (GND), U5.1 (ADDR), U5.3 (GND), U5.6 (AIN2), U5.7 (AIN3), U6.6 (VPRG2), U6.8 (GND), U6.12 (OVLO), U6.16 (GND), U6.17 (GND), U7.2 (VIN-), U7.3 (VIN-), U8.4 (GND1); also elsewhere on the board
SCL_HV: R20.1, U3.14 (SCL), U4.5 (SCL), U5.10 (SCL), U8.3 (SCL1); also elsewhere on the board
SDA_HV: R19.1, U3.15 (SDA), U4.4 (SDA), U5.9 (SDA), U8.2 (SDA1); also elsewhere on the board
SW_SCL: U8.6 (SCL2); also elsewhere on the board
SW_SDA: U8.7 (SDA2); also elsewhere on the board
~CHRG_DET: R10.2, U3.4 (P0); also elsewhere on the board
~LOW_DET: R11.1, U3.7 (P3); also elsewhere on the board

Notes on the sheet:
3.3V Linear Regulator
HIGH VOLTAGE
LOW VOLTAGE
PACK VOLTAGE SENSOR AND CHARGE SENSOR
HIGH VOLTAGE POWER
The flyback regulator responsible for delivering 5V isolated power to low voltage systems has been replaced with an isolated DC/DC converter. This is due to the insufficient output current (300mA) available when assembled. Cost is comparable.
HIGH VOLTAGE INTERFACES
HIGH VOLTAGE DIGITAL I/O
I2C PULLUP
5mA
350uA
40uA
1mA
I2C Address 0x48 (see datasheet page 14)
I2C Address 0x40 (see datasheet page 13)
This I/O expander is responsible for relaying digital signals accross the HV-LV isolation barrier via the I2C bus.
I2C ISOLATOR
This power supply is responsible for delivering non-isolated 5V power to the high voltage electronics. All AMS bus connected devices are powered from this regulator. Maximum current draw 250mA. This Switcher was selected for its high efficiency even at light load.
Maximum Current Draw on 5V output: 1.2A
Bypass Capacitor (U5)
Bypass Capacitor (U3)
Bypass Capacitor (U4)
I2C Address 0x44 (see datasheet page 18) Additional documentation of the use of this component is req'd.

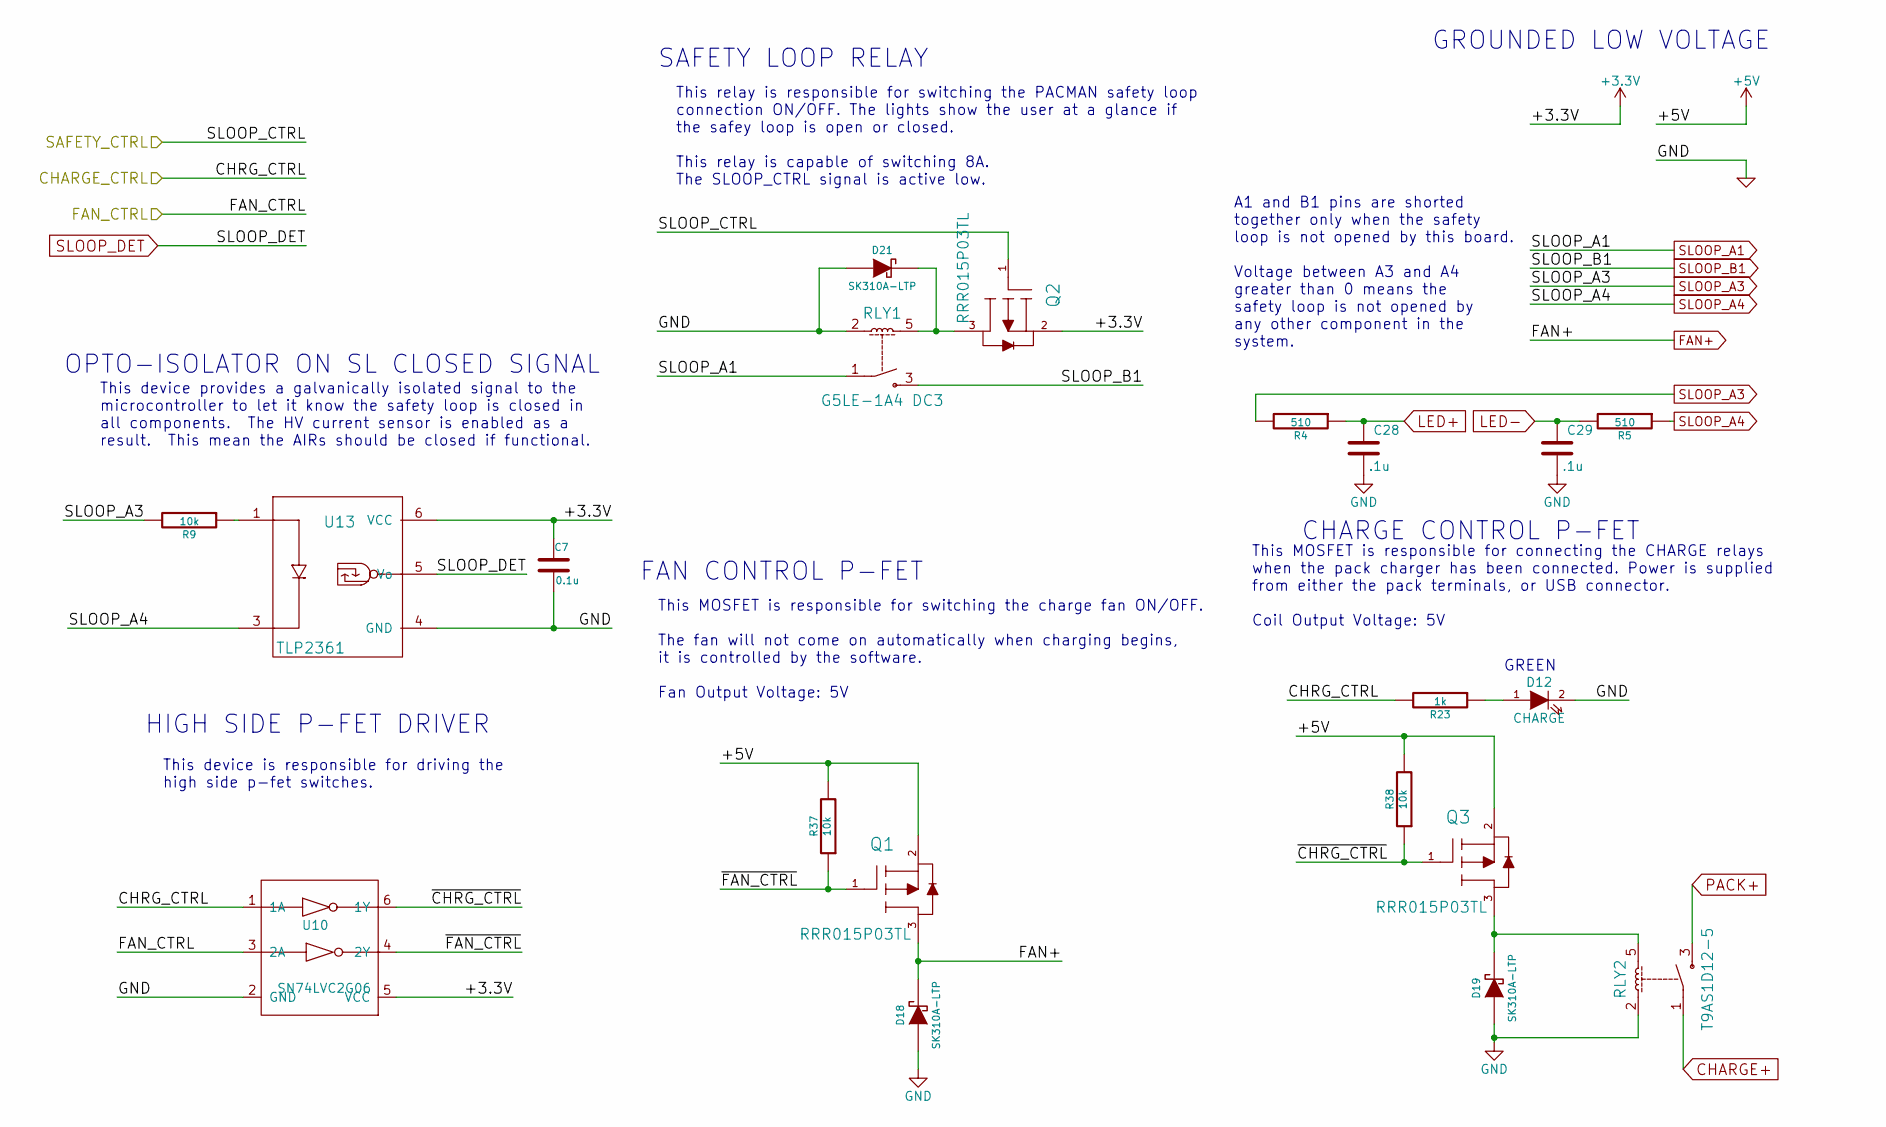
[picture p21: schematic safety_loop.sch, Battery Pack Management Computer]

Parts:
C7: 0.1u; C_0603_HandSoldering
C28, C29: .1u; C_0603_HandSoldering; Manufacturer P/N C0603C104M5RACTU
D12: CHARGE; LED_0603
D18, D19, D21: SK310A-LTP; do214ac; Manufacturer P/N SK310A-LTP
Q1, Q2, Q3: RRR015P03TL; sot346; Manufacturer P/N RRR015P03TL
R4, R5: 510; R_0805_HandSoldering; Manufacturer P/N ESR10EZPJ511
R9, R37, R38: 10k; R_0603_HandSoldering
R23: 1k; R_0603_HandSoldering
RLY1: G5LE-1A4 DC3; relay_G5LE_1A4; Manufacturer P/N G5LE-1A4 DC3
RLY2: T9AS1D12-5; RLY_T9AS1D12-5; Manufacturer P/N T9AS1D12-5
U10: SN74LVC2G06; DCK; Manufacturer P/N SN74LVC2G06DCKR
U13: TLP2361; Manufacturer P/N TLP2361(V4-TPL,E

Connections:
+3V3: C7.1, Q2.2 (D), U10.5 (VCC), U13.6 (VCC); also elsewhere on the board
+5V: Q1.2 (D), Q3.2 (D), R37.2, R38.2; also elsewhere on the board
/Safety Loop Wiring/CHARGE_CTRL: R23.2, U10.1 (1A); also elsewhere on the board
/Safety Loop Wiring/FAN_CTRL: U10.3 (2A); also elsewhere on the board
/Safety Loop Wiring/SAFETY_CTRL: Q2.1 (G); also elsewhere on the board
/Safety Loop Wiring/~CHRG_CTRL: Q3.1 (G), R38.1, U10.6 (1Y)
/Safety Loop Wiring/~FAN_CTRL: Q1.1 (G), R37.1, U10.4 (2Y)
CHARGE+: RLY2.1; also elsewhere on the board
FAN+: D18.2 (K), Q1.3 (S); also elsewhere on the board
GND: C7.2, C28.2, C29.2, D12.2 (K), D18.1 (A), D19.1 (A), D21.1 (A), RLY1.2, RLY2.2, U10.2 (GND), U13.4 (GND); also elsewhere on the board
LED+: C28.1, R4.1; also elsewhere on the board
LED-: C29.1, R5.2; also elsewhere on the board
unnamed: D12.1 (A), R23.1
unnamed: D19.2 (K), Q3.3 (S), RLY2.5
unnamed: D21.2 (K), Q2.3 (S), RLY1.5
unnamed: R9.1, U13.1
PACK+: RLY2.3; also elsewhere on the board
SLOOP_A1: RLY1.1; also elsewhere on the board
SLOOP_A3: R4.2, R9.2; also elsewhere on the board
SLOOP_A4: R5.1, U13.3; also elsewhere on the board
SLOOP_B1: RLY1.3; also elsewhere on the board
SLOOP_DET: U13.5 (Vo); also elsewhere on the board

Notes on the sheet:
CHARGE CONTROL P-FET
SAFETY LOOP RELAY
This relay is responsible for switching the PACMAN safety loop connection ON/OFF. The lights show the user at a glance if the safey loop is open or closed. This relay is capable of switching 8A. The SLOOP_CTRL signal is active low.
This MOSFET is responsible for connecting the CHARGE relays when the pack charger has been connected. Power is supplied from either the pack terminals, or USB connector. Coil Output Voltage: 5V
FAN CONTROL P-FET
This MOSFET is responsible for switching the charge fan ON/OFF. The fan will not come on automatically when charging begins, it is controlled by the software. Fan Output Voltage: 5V
GROUNDED LOW VOLTAGE
GREEN
This device is responsible for driving the high side p-fet switches.
HIGH SIDE P-FET DRIVER
A1 and B1 pins are shorted together only when the safety loop is not opened by this board. Voltage between A3 and A4 greater than 0 means the safety loop is not opened by any other component in the system.
OPTO-ISOLATOR ON SL CLOSED SIGNAL
This device provides a galvanically isolated signal to the microcontroller to let it know the safety loop is closed in all components. The HV current sensor is enabled as a result. This mean the AIRs should be closed if functional.

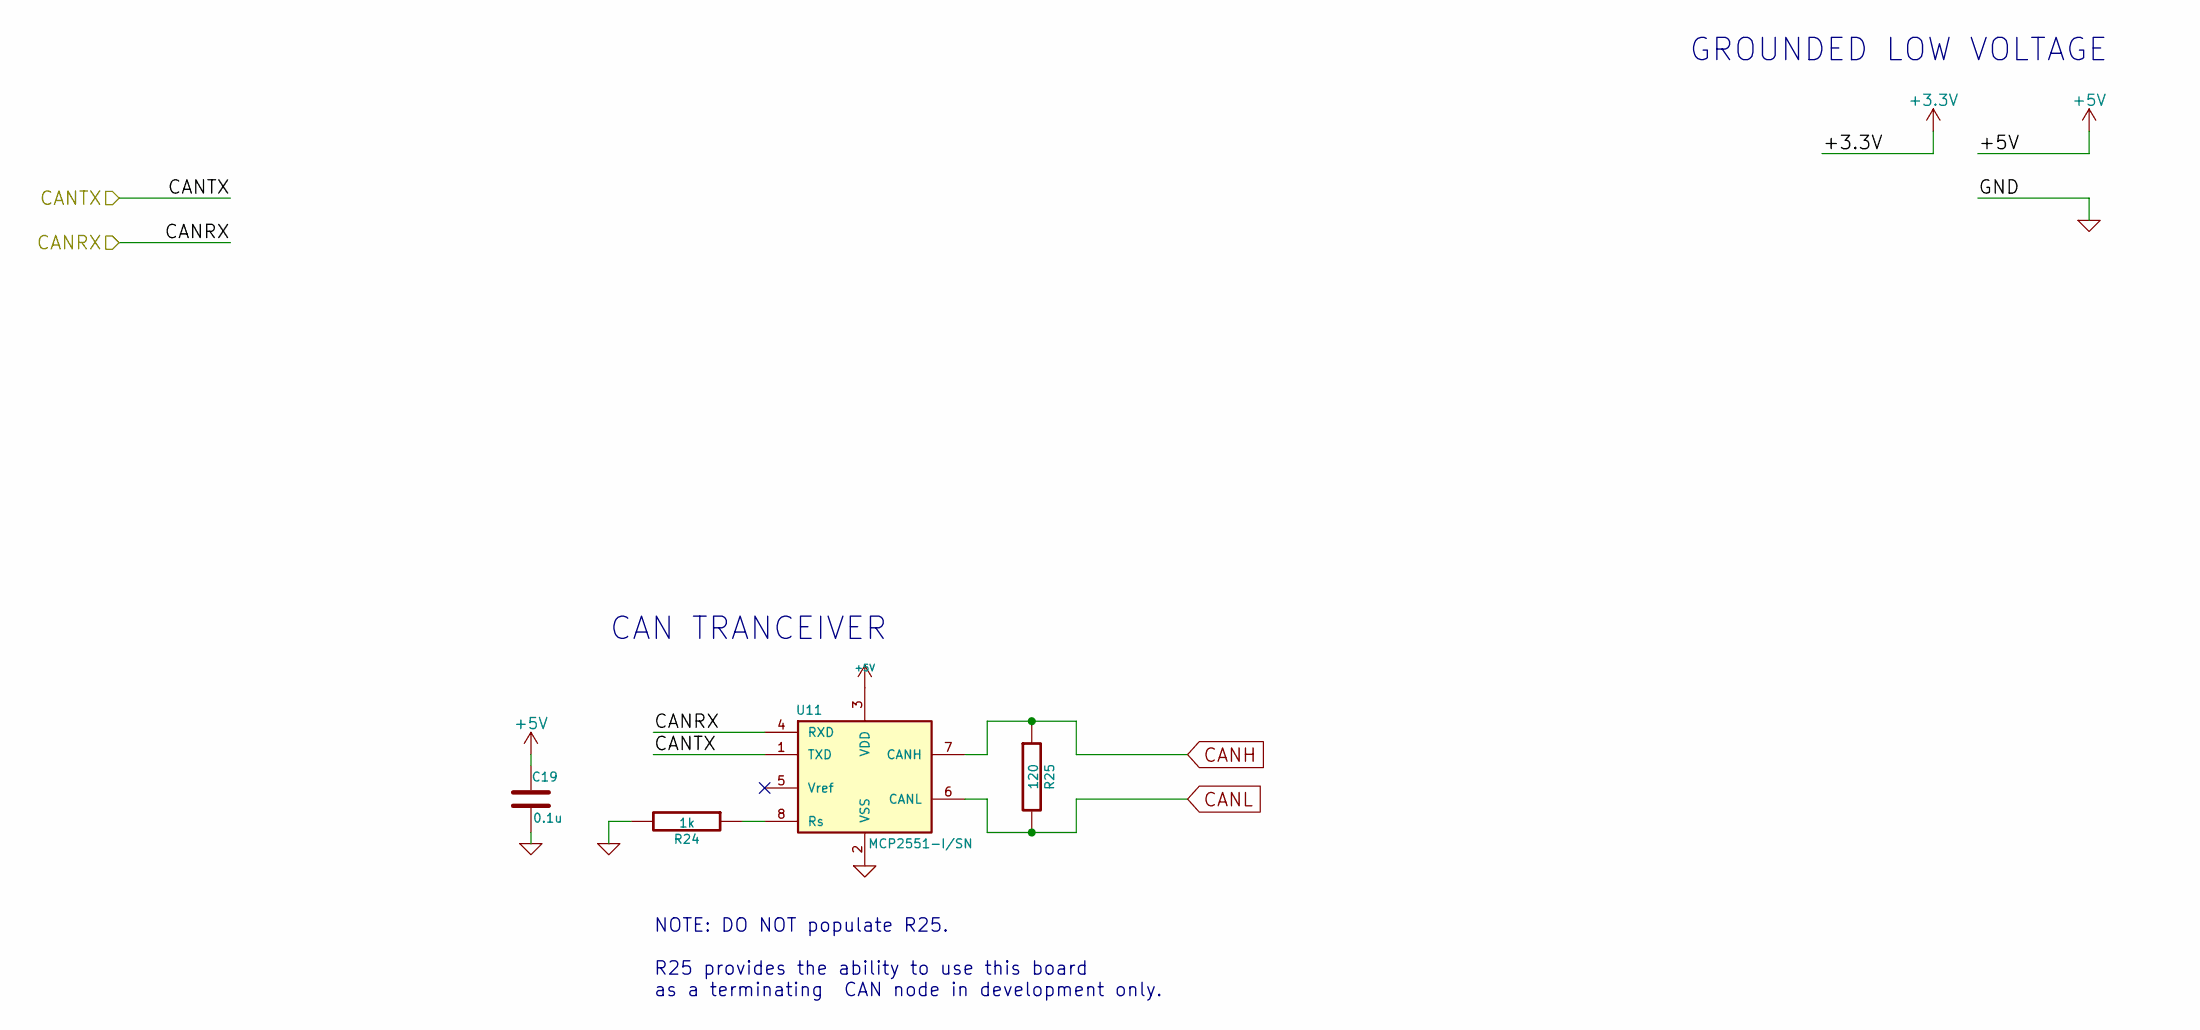
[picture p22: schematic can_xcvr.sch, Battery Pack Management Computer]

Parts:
C19: 0.1u; C_0603_HandSoldering
R24: 1k; R_0603_HandSoldering
R25: 120; R_0805_HandSoldering
U11: MCP2551-I/SN; SOIC-8_3.9x4.9mm_Pitch1.27mm; Manufacturer P/N MCP2551-I/SN

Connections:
+5V: C19.1, U11.3 (VDD); also elsewhere on the board
/CAN Transceiver/CANRX: U11.4 (RXD); also elsewhere on the board
/CAN Transceiver/CANTX: U11.1 (TXD); also elsewhere on the board
CANH: R25.1, U11.7 (CANH); also elsewhere on the board
CANL: R25.2, U11.6 (CANL); also elsewhere on the board
GND: C19.2, R24.2, U11.2 (VSS); also elsewhere on the board
unnamed: R24.1, U11.8 (Rs)

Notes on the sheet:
CAN TRANCEIVER
NOTE: DO NOT populate R25. R25 provides the ability to use this board as a terminating CAN node in development only.
GROUNDED LOW VOLTAGE

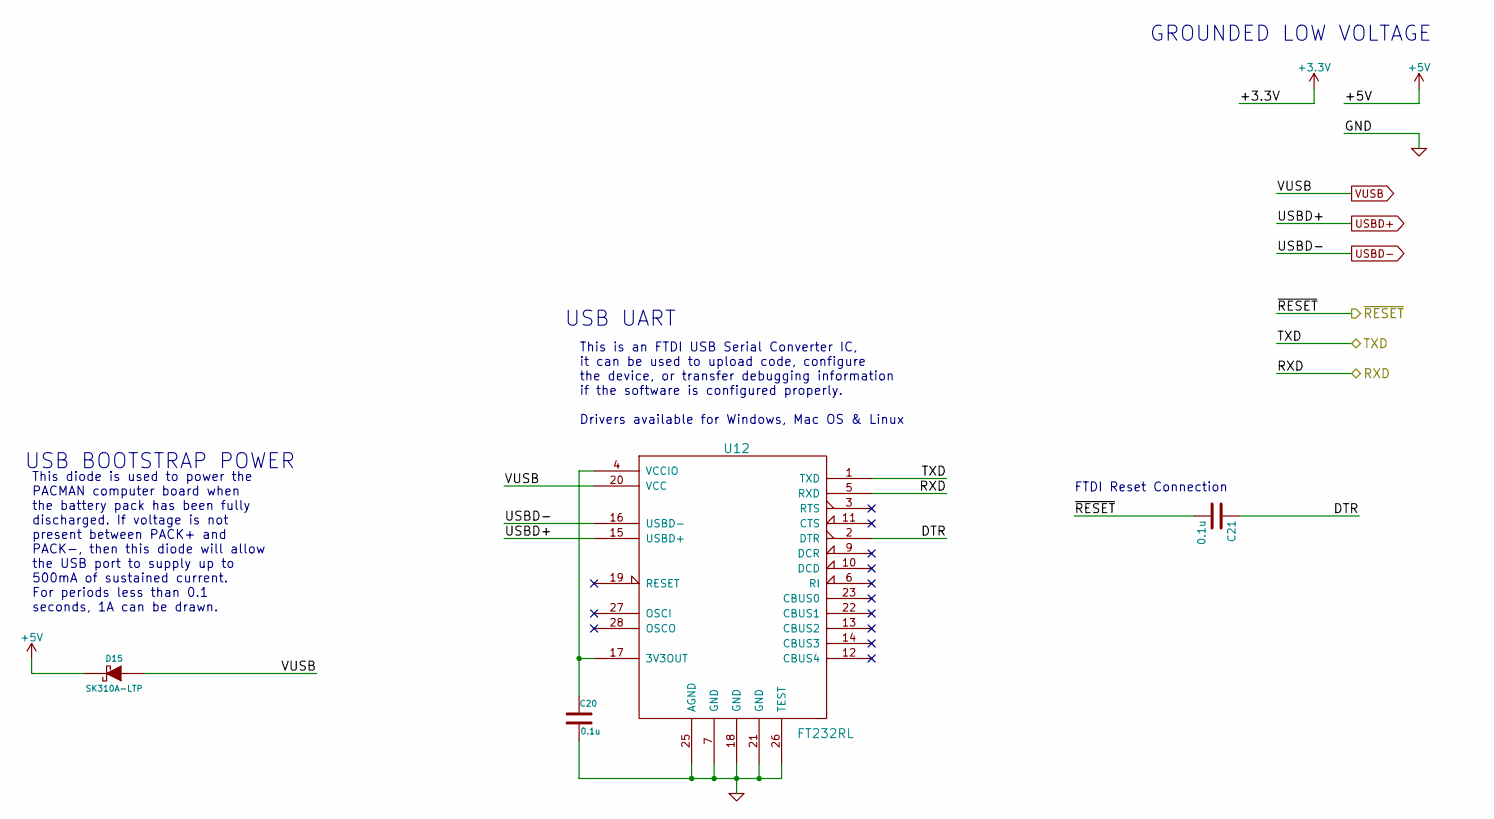
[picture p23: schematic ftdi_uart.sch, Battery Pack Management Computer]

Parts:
C20, C21: 0.1u; C_0603_HandSoldering
D15: SK310A-LTP; do214ac; Manufacturer P/N SK310A-LTP
U12: FT232RL; SSOP-28_5.3x10.2mm_Pitch0.65mm; Manufacturer P/N FT232RL-REEL

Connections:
+5V: D15.2 (K); also elsewhere on the board
/FTDI USB UART/DTR: C21.1, U12.2 (DTR)
/FTDI USB UART/RXD: U12.5 (RXD); also elsewhere on the board
/FTDI USB UART/TXD: U12.1 (TXD); also elsewhere on the board
GND: C20.2, U12.7 (GND), U12.18 (GND), U12.21 (GND), U12.25 (AGND), U12.26 (TEST); also elsewhere on the board
unnamed: C20.1, U12.4 (VCCIO), U12.17 (3V3OUT)
USBD+: U12.15 (USBD+); also elsewhere on the board
USBD-: U12.16 (USBD-); also elsewhere on the board
VUSB: D15.1 (A), U12.20 (VCC); also elsewhere on the board
~RESET_AVR: C21.2; also elsewhere on the board

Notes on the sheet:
FTDI Reset Connection
USB UART
USB BOOTSTRAP POWER
This diode is used to power the PACMAN computer board when the battery pack has been fully discharged. If voltage is not present between PACK+ and PACK-, then this diode will allow the USB port to supply up to 500mA of sustained current. For periods less than 0.1 seconds, 1A can be drawn.
This is an FTDI USB Serial Converter IC, it can be used to upload code, configure the device, or transfer debugging information if the software is configured properly. Drivers available for Windows, Mac OS & Linux
GROUNDED LOW VOLTAGE

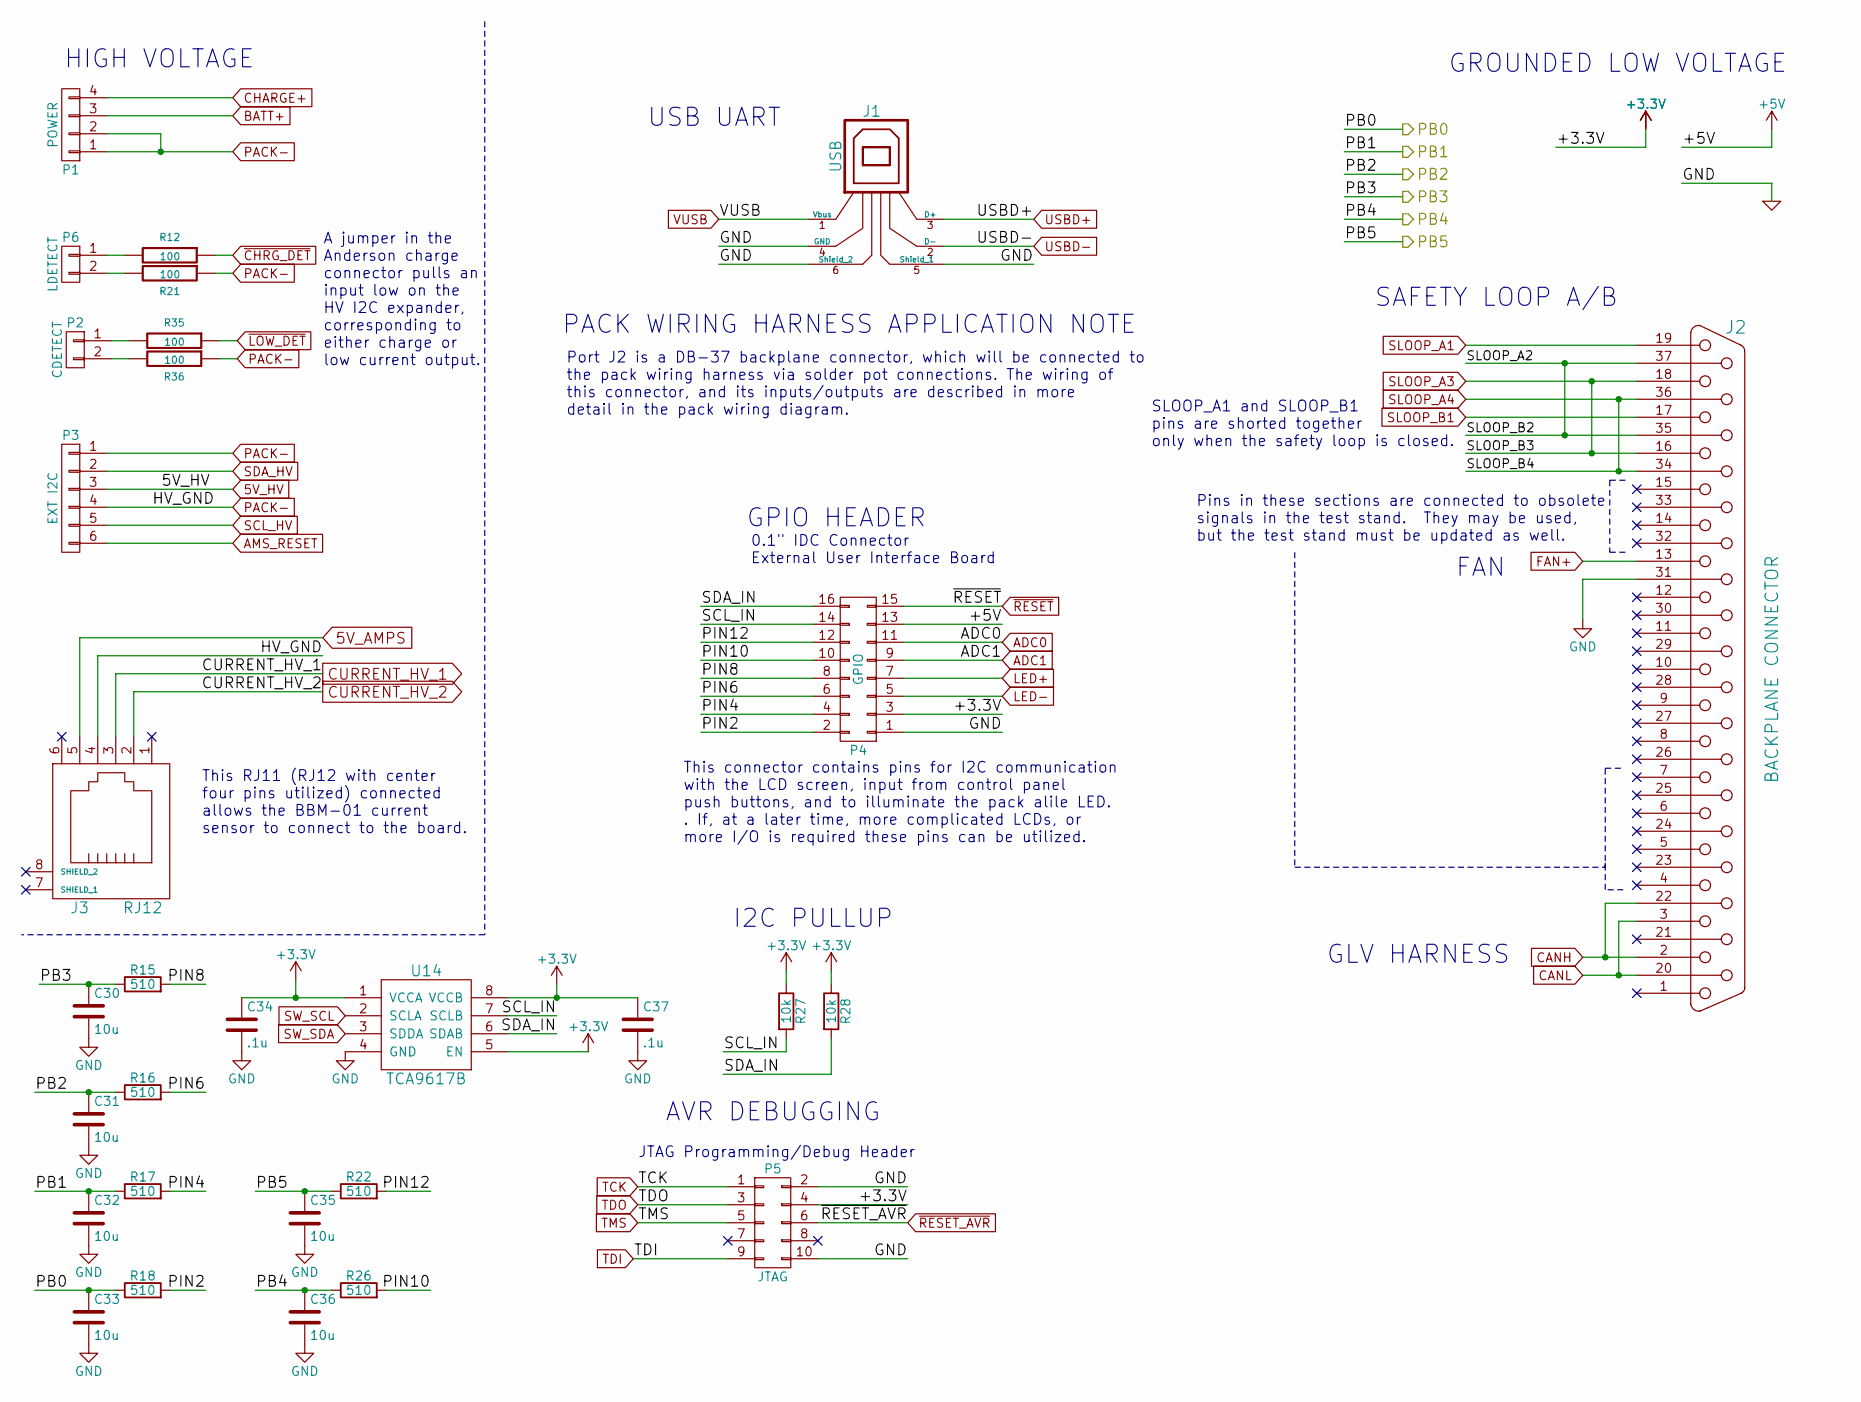
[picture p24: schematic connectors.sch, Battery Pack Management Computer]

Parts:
C30, C31, C32, C33, C35, C36: 10u; C_0805_HandSoldering; Manufacturer P/N CL21A106KQCLRNC
C34, C37: .1u; C_0603_HandSoldering; Manufacturer P/N GRM21BR71E104KA01L
J1: USB; conn_usb_B; Manufacturer P/N 1734346-1
J2: BACKPLANE CONNECTOR; DB37FD; Manufacturer P/N 171-037-213R011
J3: RJ12; MOLEX_RJ11; Manufacturer P/N 0855135002
P1: POWER; AMPCONN_4POS; Manufacturer P/N 556881-4
P2: CDETECT; MOLEX_HEADER_2POS; Manufacturer P/N 15-91-2025
P3: EXT I2C; MOLEX_HEADER_6POS; Manufacturer P/N 15-91-2065
P4: GPIO; IDC_Header_Straight_16pins; Manufacturer P/N 30316-6002HB
P5: JTAG; Manufacturer P/N 20021521-00010T1LF
P6: LDETECT; MOLEX_HEADER_2POS; Manufacturer P/N 15-91-2025
R12, R21, R35, R36: 100; R_0603_HandSoldering
R15, R16, R17, R18, R22, R26: 510; R_0603_HandSoldering; Manufacturer P/N RMCF0805JT510R
R27, R28: 10k; R_0603_HandSoldering
U14: TCA9617B; Manufacturer P/N TCA9617BDGKR

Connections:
5V_AMPS: J3.5; also elsewhere on the board
5V_HV: P3.3; also elsewhere on the board
+3V3: C34.1, C37.1, P4.3, P5.4, R27.1, R28.1, U14.1 (VCCA), U14.5 (EN), U14.8 (VCCB); also elsewhere on the board
+5V: P4.13; also elsewhere on the board
/External Connectors/PB0: C33.1, R18.1; also elsewhere on the board
/External Connectors/PB1: C32.1, R17.1; also elsewhere on the board
/External Connectors/PB2: C31.1, R16.1; also elsewhere on the board
/External Connectors/PB3: C30.1, R15.1; also elsewhere on the board
/External Connectors/PB4: C36.1, R26.1; also elsewhere on the board
/External Connectors/PB5: C35.1, R22.1; also elsewhere on the board
/External Connectors/PIN2: P4.2, R18.2
/External Connectors/PIN4: P4.4, R17.2
/External Connectors/PIN6: P4.6, R16.2
/External Connectors/PIN8: P4.8, R15.2
/External Connectors/PIN10: P4.10, R26.2
/External Connectors/PIN12: P4.12, R22.2
/External Connectors/SCL_IN: P4.14, R27.2, U14.7 (SCLB)
/External Connectors/SDA_IN: P4.16, R28.2, U14.6 (SDAB)
/External Connectors/SLOOP_A2: J2.35, J2.37
ADC0: P4.11; also elsewhere on the board
ADC1: P4.9; also elsewhere on the board
AMS_RESET: P3.6; also elsewhere on the board
BATT+: P1.3; also elsewhere on the board
CANH: J2.2, J2.22; also elsewhere on the board
CANL: J2.3, J2.20; also elsewhere on the board
CHARGE+: P1.4; also elsewhere on the board
CURRENT_HV_1: J3.3; also elsewhere on the board
CURRENT_HV_2: J3.2; also elsewhere on the board
FAN+: J2.13; also elsewhere on the board
GND: C30.2, C31.2, C32.2, C33.2, C34.2, C35.2, C36.2, C37.2, J1.4 (GND), J1.5 (Shield_1), J1.6 (Shield_2), J2.31, P4.1, P5.2, P5.10, U14.4 (GND); also elsewhere on the board
LED+: P4.7; also elsewhere on the board
LED-: P4.5; also elsewhere on the board
unnamed: P2.1, R35.2
unnamed: P2.2, R36.2
unnamed: P6.1, R12.2
unnamed: P6.2, R21.2
PACK-: J3.4, P1.1, P1.2, P3.1, P3.4, R21.1, R36.1; also elsewhere on the board
SCL_HV: P3.5; also elsewhere on the board
SDA_HV: P3.2; also elsewhere on the board
SLOOP_A1: J2.19; also elsewhere on the board
SLOOP_A3: J2.16, J2.18; also elsewhere on the board
SLOOP_A4: J2.34, J2.36; also elsewhere on the board
SLOOP_B1: J2.17; also elsewhere on the board
SW_SCL: U14.2 (SCLA); also elsewhere on the board
SW_SDA: U14.3 (SDDA); also elsewhere on the board
TCK: P5.1; also elsewhere on the board
TDI: P5.9; also elsewhere on the board
TDO: P5.3; also elsewhere on the board
TMS: P5.5; also elsewhere on the board
USBD+: J1.3 (D+); also elsewhere on the board
USBD-: J1.2 (D-); also elsewhere on the board
VUSB: J1.1 (Vbus); also elsewhere on the board
~CHRG_DET: R12.1; also elsewhere on the board
~LOW_DET: R35.1; also elsewhere on the board
~RESET: P4.15; also elsewhere on the board
~RESET_AVR: P5.6; also elsewhere on the board

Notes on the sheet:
HIGH VOLTAGE
USB UART
AVR DEBUGGING
JTAG Programming/Debug Header
0.1" IDC Connector External User Interface Board
GPIO HEADER
This connector contains pins for I2C communication with the LCD screen, input from control panel push buttons, and to illuminate the pack alile LED. . If, at a later time, more complicated LCDs, or more I/O is required these pins can be utilized.
GROUNDED LOW VOLTAGE
FAN
SLOOP_A1 and SLOOP_B1 pins are shorted together only when the safety loop is closed.
GLV HARNESS
SAFETY LOOP A/B
PACK WIRING HARNESS APPLICATION NOTE
Port J2 is a DB-37 backplane connector, which will be connected to the pack wiring harness via solder pot connections. The wiring of this connector, and its inputs/outputs are described in more detail in the pack wiring diagram.
This RJ11 (RJ12 with center four pins utilized) connected allows the BBM-01 current sensor to connect to the board.
A jumper in the Anderson charge connector pulls an input low on the HV I2C expander, corresponding to either charge or low current output.
Pins in these sections are connected to obsolete signals in the test stand. They may be used, but the test stand must be updated as well.
I2C PULLUP

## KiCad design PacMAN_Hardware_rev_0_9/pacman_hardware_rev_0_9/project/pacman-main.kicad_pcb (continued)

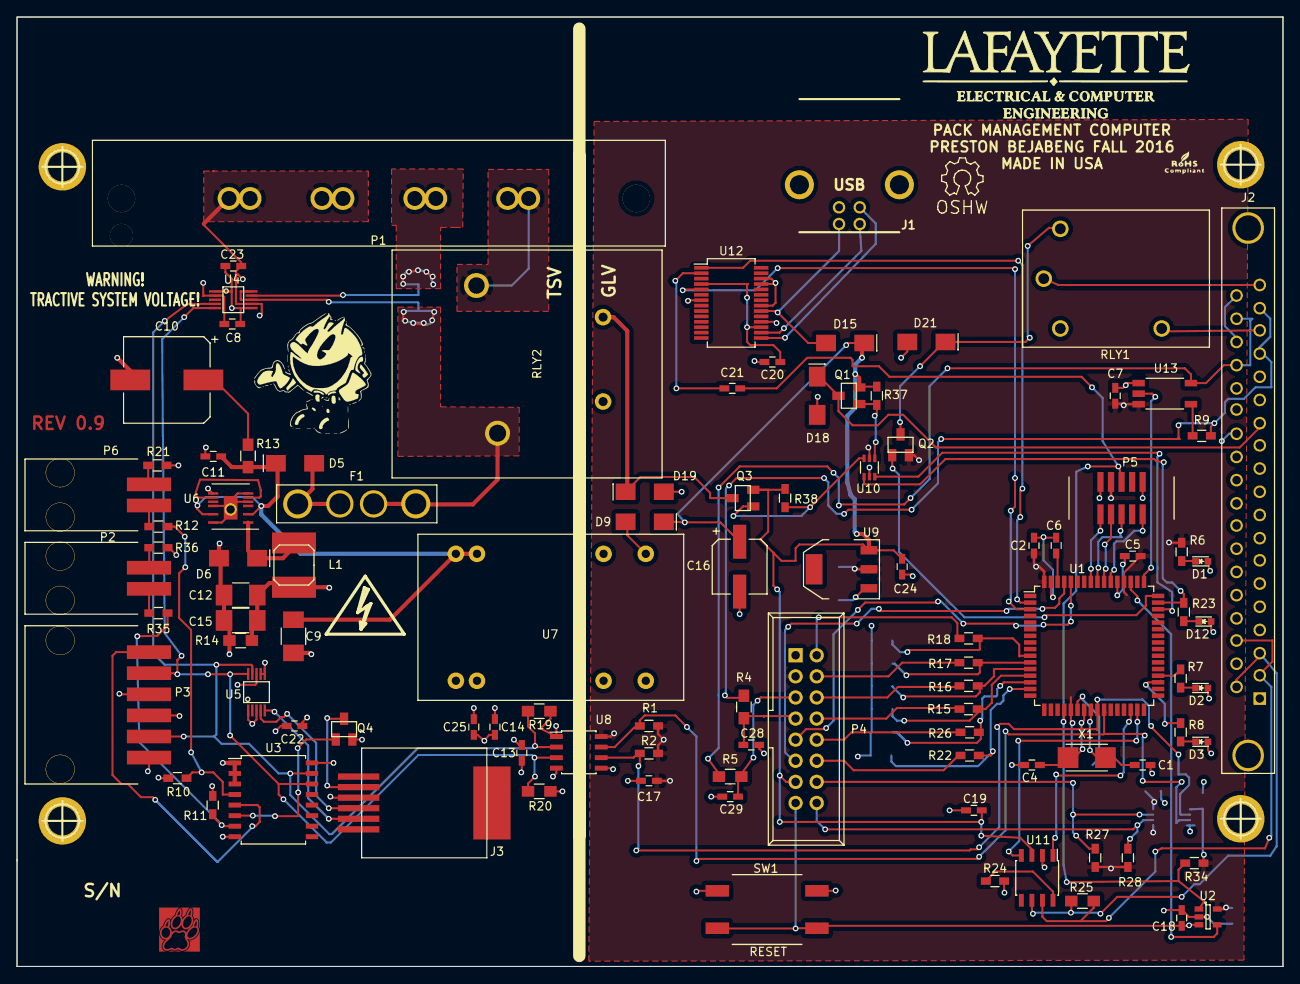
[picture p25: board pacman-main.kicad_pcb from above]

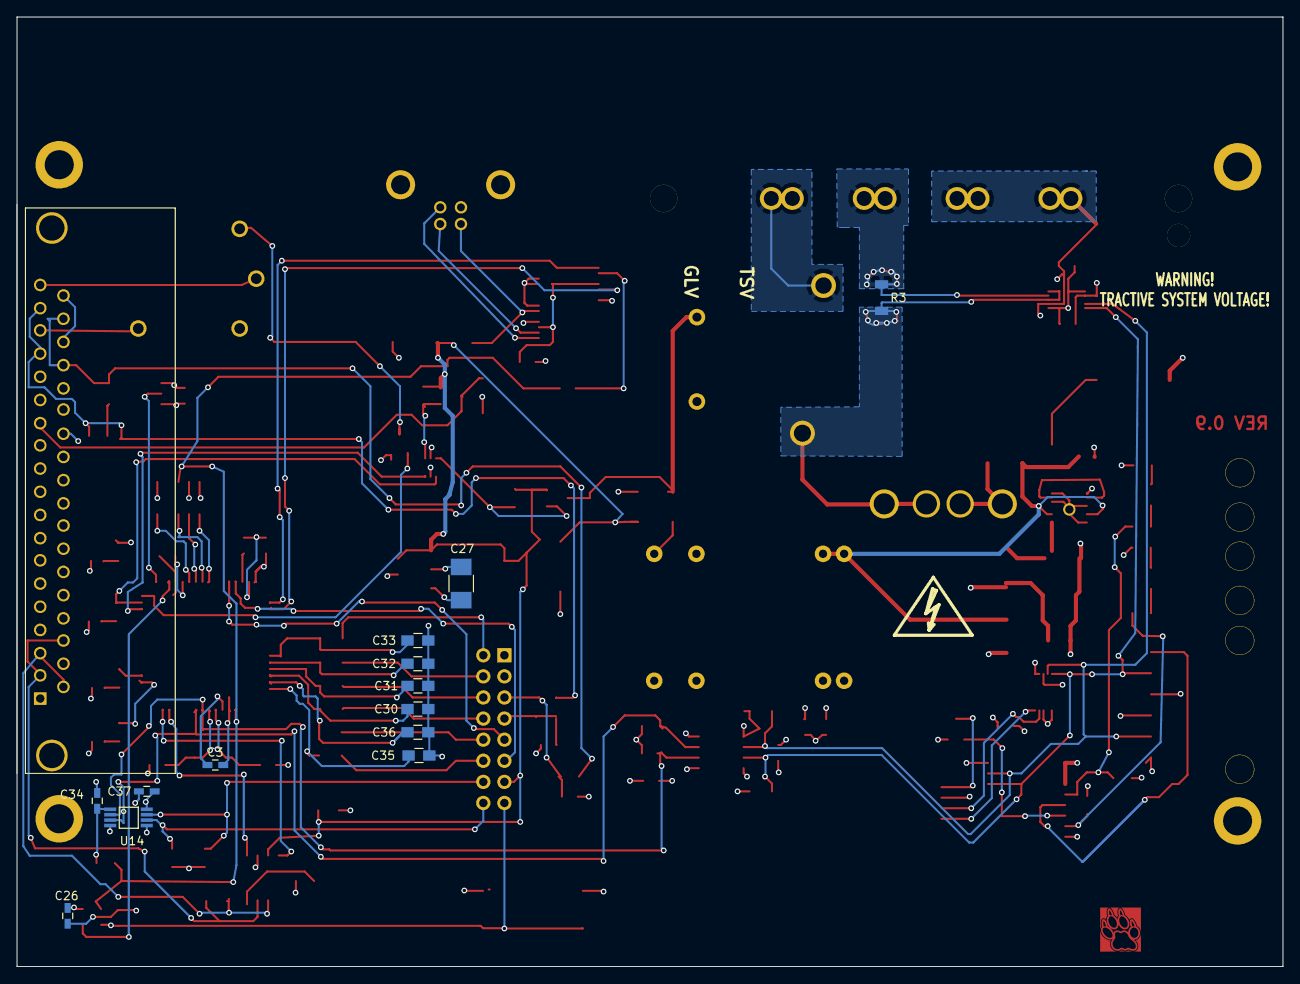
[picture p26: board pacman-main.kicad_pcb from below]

Board: 4 copper layers, 152.4 x 114.3 mm, 119 parts (13 on the bottom side), 90 nets.

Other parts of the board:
VAL: REF; lafLogo
hole_3mm5, hole_3mm5#2, hole_3mm5#3, hole_3mm5#4: VAL**; hole_3mm5

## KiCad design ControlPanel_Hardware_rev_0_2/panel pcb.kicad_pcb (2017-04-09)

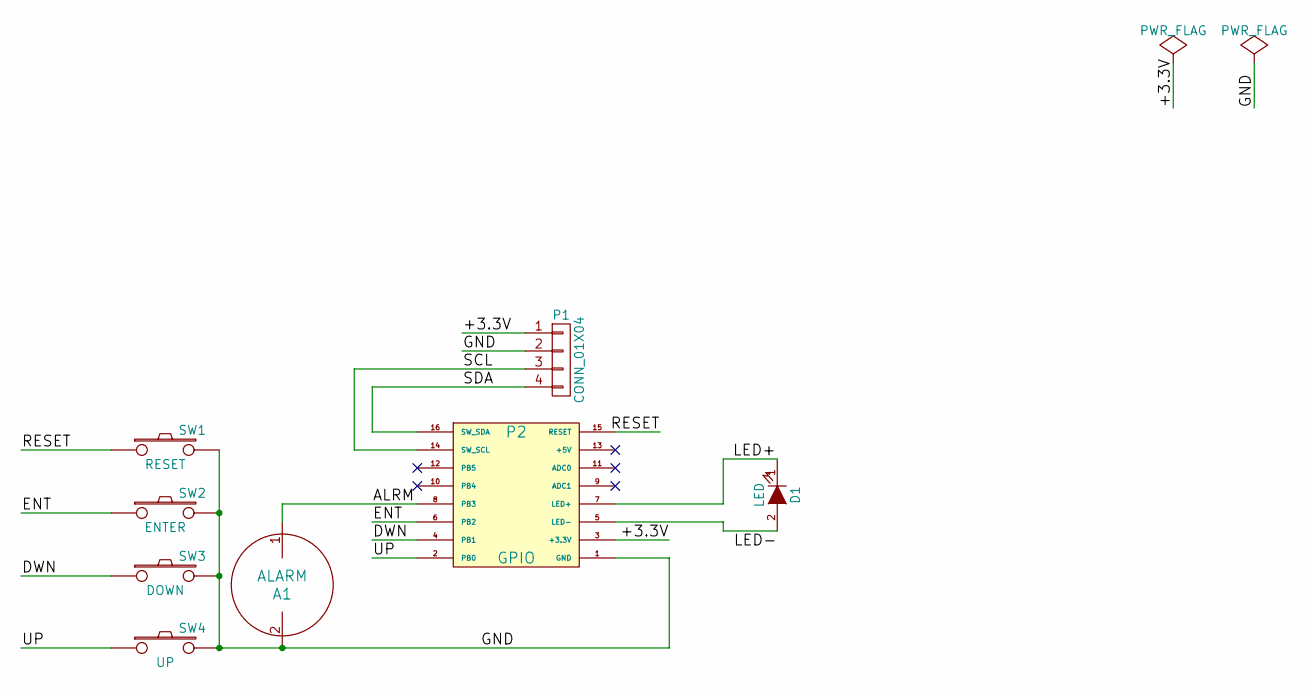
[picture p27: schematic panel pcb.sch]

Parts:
A1: ALARM; Manufacturer PN AI-1027-TWT-5V-2-R
D1: LED; LED_D5.0mm; Manufacturer P/N WP56BSRD/B
P1: CONN_01X04; MOLEX4Vert
P2: GPIO; IDC_Header_Straight_16pins
SW1: RESET; SW_RACON_8; Manufacturer PN 1.14100.5030000
SW2: ENTER; SW_RACON_8; Manufacturer PN 1.14100.5030000
SW3: DOWN; SW_RACON_8; Manufacturer PN 1.14100.5030000
SW4: UP; SW_RACON_8; Manufacturer PN 1.14100.5030000

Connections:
/+3.3V: P1.1, P2.3 (+3.3V)
/ALRM: A1.1, P2.8 (PB3)
/DWN: P2.4 (PB1), SW3.1
/ENT: P2.6 (PB2), SW2.1
/GND: A1.2, P1.2, P2.1 (GND), SW1.2, SW2.2, SW3.2, SW4.2
/LED+: D1.1 (K), P2.7 (LED+)
/RESET: P2.15 (RESET), SW1.1
/SCL: P1.3, P2.14 (SW_SCL)
/SDA: P1.4, P2.16 (SW_SDA)
/UP: P2.2 (PB0), SW4.1
unnamed: D1.2 (A), P2.5 (LED-)

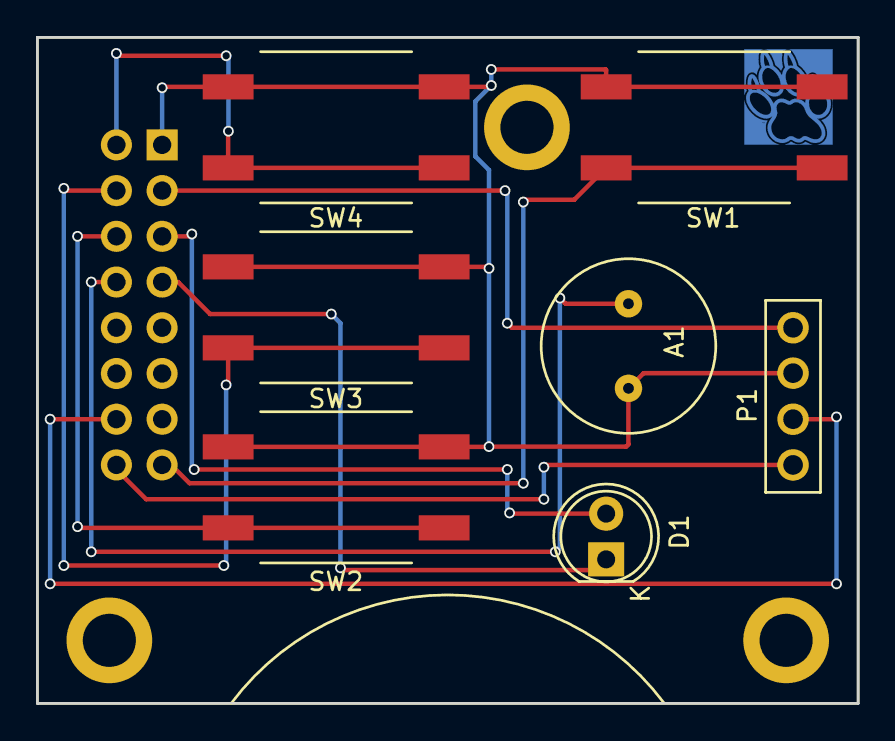
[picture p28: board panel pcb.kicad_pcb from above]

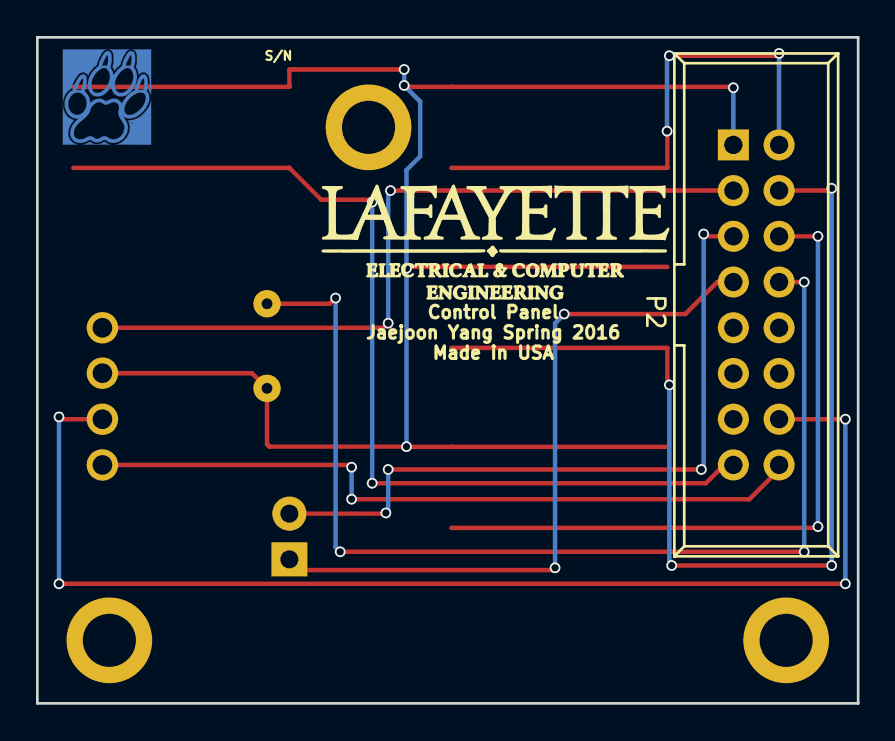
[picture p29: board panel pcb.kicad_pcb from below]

Board: 2 copper layers, 45.6 x 37.0 mm, 9 parts (2 on the bottom side), 11 nets.

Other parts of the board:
VAL: REF; lafLogo

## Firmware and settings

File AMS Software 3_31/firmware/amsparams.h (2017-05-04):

#ifndef AMSPARAMS_H
#define AMSPARAMS_H

// device input/outputs
#define MCLR    LATAbits.LATA5  // pin RA5
#define ACTLED  LATAbits.LATA6  // pin RA6
#define BYPASS  LATBbits.LATB0  // pin RB0
#define SDA1    LATBbits.LATB1  // pin RB1
#define SCL1    LATBbits.LATB4  // pin RB4
#define ICSPCLK LATBbits.LATB6  // pin RB6
#define ICSPDAT LATBbits.LATB7  // pin RB7

// command values
#define CLR_BY           0x00
#define SET_BY           0x01
#define PANIC            0x02
#define RELAX            0x03
#define SET_ADDR         0x04
#define SET_BYTIME       0x05
#define SET_V_CAL        0x06
#define SET_SERIAL       0x07
#define CHANGE_READ_TYPE 0x30

// i2c read types
#define READ_VOLTAGE  0x00
#define READ_SERIAL   0x01
#define READ_CAL_DATA 0x02
#define READ_MAGIC    0x03

// EEPROM parameters
#define DEFAULT_ADDR   (0x04 << 2)  // default I2C address
#define DEFAULT_BYTIME 0x00FF       // default bypass time
#define DEFAULT_V_CAL  0x00000000   // defauult cell voltage calibration
#define EEPROM_ADDR    1            // slave_id memory location
#define EEPROM_BYTIME  2            // location of the bypass limit (2 bytes)
#define EEPROM_V_CAL   4            // location of voltage calibration info (4 bytes)
#define EEPROM_SERIAL  8            // location of the serial number (4 bytes)

// adc multiplexer enumeration
#define ADC_WAIT    0
#define ADC_VOLT    1
#define ADC_TEMP    2

// adc channels of connected devices
#define ADC_CHAN_VOLT  10
#define ADC_CHAN_TEMP   9

// preprocessor pin numbers
#define PIN_0    0
#define PIN_1    1
#define PIN_2    2
#define PIN_3    3
#define PIN_4    4
#define PIN_5    5
#define PIN_6    6
#define PIN_7    7

#endif /*AMSPARAMS_H*/

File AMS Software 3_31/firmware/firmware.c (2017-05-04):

/******************************************************************************
 *  Filename:       firmware.c
 *  Date:           09/29/15
 *  File Verison:   3.0
 *
 *  Authors:        Alex Hytha     (LFEV'15 4/03/15)
 *                  John Gehrig    (LFEV'15 09/29/15)
 *                  
 *  Team:           LFEV'15
 *
 * ****************************************************************************
 *  Architecture:   Enhanced Midrange PIC
 *  Processor:      PIC16LF1827
 *  Compiler:       MPLAB X XC8
 *
 * ****************************************************************************
 *  Description:    Firmware for the slave pic
 *
 * ****************************************************************************
 *  Pin Assignments: FIXME
 *      LEDS:
 *          RA6 -- PLED
 *          RA7 -- WDT LED (not implemented on the BMS board)
 *          RB0 -- Bypass LED
 *
 *      ANALOG INPUT CHANNELS:
 *          RB2/AN10 --  Temp
 *          RB3/AN9  --  Volt
 *
 *****************************************************************************/

#include "config.h"
#include "amsparams.h"

#include <xc.h>
#include <stdint.h>

#include "adc.h"
#include "i2c.h"
#include "watchdog.h"
#include "eeprom.h"

/**
 * 
 */
void setup() {
	// clear ports A and B
	LATA = 0x00;
	LATB = 0x00;
	
	// set the pin input/output directions
	TRISA  = (1 << PIN_5);
	TRISB  = (1 << PIN_1) |
			 (1 << PIN_2) |
			 (1 << PIN_3) |
			 (1 << PIN_4);


	// set up the ADC ports
	ANSELB = (1 << PIN_2) |
			 (1 << PIN_3);
	//
	// CHECK EEPROM
	//
	i2c_address = read_eeprom(EEPROM_ADDR);

	if((i2c_address == 0x00) || (i2c_address == 0xFF)) {
		write_eeprom(EEPROM_ADDR, DEFAULT_ADDR);
		i2c_address = read_eeprom(EEPROM_ADDR);
	}

	// load the bypass limit from memory
	bypass_limit =
			(read_eeprom(EEPROM_BYTIME) << 8) |
			(read_eeprom(EEPROM_BYTIME + 1));
	if((bypass_limit == 0x00) || (bypass_limit == 0xFF)) {
		write_eeprom(EEPROM_ADDR, DEFAULT_BYTIME);
		bypass_limit =
				(read_eeprom(EEPROM_BYTIME) << 8) |
				(read_eeprom(EEPROM_BYTIME + 1));
	}

	        // serial code data
                serial[3] = read_eeprom(EEPROM_SERIAL);
                serial[2] = read_eeprom(EEPROM_SERIAL + 1);
                serial[1] = read_eeprom(EEPROM_SERIAL + 2);
                serial[0] = read_eeprom(EEPROM_SERIAL + 3);

                // calibration data
                cal_data[3] = read_eeprom(EEPROM_V_CAL);
                cal_data[2] = read_eeprom(EEPROM_V_CAL + 1);
                cal_data[1] = read_eeprom(EEPROM_V_CAL + 2);
                cal_data[0] = read_eeprom(EEPROM_V_CAL + 3);
                // Update slope and offset values
                slope  = (cal_data[3] << 8) | cal_data[2];
                offset = (cal_data[1] << 8) | cal_data[0];

                // set read type to default (voltage/temp)
                read_type = READ_VOLTAGE;
                
	// initialize the watchdog timer
	init_WDT();
	
	// initialize the I2C bus
	init_I2C(i2c_address);
	
	// initialize the ADC
	init_ADC();
}

/**
 * 
 */
void interrupt ISR(void) {
	// disable global and peripheral interrupts
	INTCONbits.GIE  = 0;
	INTCONbits.PEIE = 0;

	// handle the I2C interrupt 
	if( PIR1bits.SSP1IF ) I2C_ISR();

	// handle the ADC interrupt 
	if( PIR1bits.ADIF ) ADC_ISR();
	
	// enable global and peripheral interrupts
	INTCONbits.GIE = 1;
	INTCONbits.PEIE = 1;
}

/**
 * 
 */
int main(void){
	// the following is disabled because a 1MHz system clock uses less power
	// delays 10 cycles, then switches to internal 8 MHz Clock
	//_delay(10);
	//OSCCON = 0x72;

	// initialize the slave PIC, enable interrupts
	setup();   
	
	// enable global and peripheral interrupts
	INTCONbits.PEIE = 1;
	INTCONbits.GIE  = 1;

	// act led state for PANIC command
	bool panic_led = 0;

	// save power while waiting for interrupts
	while(1) {
		// place PIC in sleep mode
		SLEEP();

		// WDT wakeup occured, handle
		event_wdt();

		// bug, gpio set in the isr does not stay set
		// ternary operator must be used, simply setting bypass
		// to bypass flag also causes this same error(cleared value)
		// panic flag behaves in the same way, setting ACTLED to 
		// the below expression (panic_led) does not work.
		// The intermediary panic_led variable must be used.
		//
		// seems like an optimizer error to me, volatile is being used
		//
		// XC8 v1.35 & v1.12 tested (both same problem)
		// Engineer: John Gehrig
		panic_led = (panic_flag) ? ~panic_led : 0;
		BYPASS = bypass_flag;
		ACTLED = (panic_flag) ? panic_led : 0;
	}
	
	return 0;
}

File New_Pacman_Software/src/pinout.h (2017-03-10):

#ifndef PINOUT_H
#define PINOUT_H

#define GPIO_INPUT          0b00
#define GPIO_INPUT_PULLUP   0b01
#define GPIO_OUTPUT_LOW     0b10
#define GPIO_OUTPUT_HIGH    0b11

/**
* @name 
* @{ */
#define HIGH  1
#define LOW   0
/**  @} */

/**
* @brief 
*/
typedef struct {
	void* prt_reg,
	void* ddr_reg,
	void* pin_reg,
	uint8_t pin_num,
} GPIO_PIN;


/**
* @name 
* @{ */
// PORTA gpio pins
static const GPIO_PIN WATCHDOG    =  {&PORTA, &DDRA, &PINA, 0};
static const GPIO_PIN SW_SDA      =  {&PORTA, &DDRA, &PINA, 1};
static const GPIO_PIN SW_SCL      =  {&PORTA, &DDRA, &PINA, 2};
static const GPIO_PIN SLOOP_CTRL  =  {&PORTA, &DDRA, &PINA, 3};
static const GPIO_PIN CHRG_CTRL   =  {&PORTA, &DDRA, &PINA, 4};
static const GPIO_PIN FAN_CTRL    =  {&PORTA, &DDRA, &PINA, 5};

// PORTB gpio pins
static const GPIO_PIN GPIO_PB0    =  {&PORTB, &DDRB, &PINB, 0};
static const GPIO_PIN GPIO_PB1    =  {&PORTB, &DDRB, &PINB, 1};
static const GPIO_PIN GPIO_PB2    =  {&PORTB, &DDRB, &PINB, 2};
static const GPIO_PIN GPIO_PB3    =  {&PORTB, &DDRB, &PINB, 3};
static const GPIO_PIN GPIO_PB4    =  {&PORTB, &DDRB, &PINB, 4};
static const GPIO_PIN GPIO_PB5    =  {&PORTB, &DDRB, &PINB, 5};
static const GPIO_PIN GPIO_PB6    =  {&PORTB, &DDRB, &PINB, 6};
static const GPIO_PIN GPIO_PB7    =  {&PORTB, &DDRB, &PINB, 7};

// PORTC gpio pins
static const GPIO_PIN FAULT       =  {&PORTC, &DDRC, &PINC, 0};
static const GPIO_PIN REQUEST     =  {&PORTC, &DDRC, &PINC, 1};
static const GPIO_PIN LOW_VOLT    =  {&PORTC, &DDRC, &PINC, 2};

// PORTF gpio pins
static const GPIO_PIN GPIO_ADC0   =  {&PORTF, &DDRF, &PINF, 0};
static const GPIO_PIN GPIO_ADC1   =  {&PORTF, &DDRF, &PINF, 1};
static const GPIO_PIN GPIO_ADC2   =  {&PORTF, &DDRF, &PINF, 2};
static const GPIO_PIN GPIO_ADC3   =  {&PORTF, &DDRF, &PINF, 3};
/**  @} */


/**
* @brief 
*
* @param pin
* @param mode
*/
static inline void pinMode(GPIO_PIN pin, uint8_t mode) {
	*(pin.ddr_reg) = 
}


/**
* @brief 
*
* @param pin
* @param value
*/
static inline void pinWrite(GPIO_PIN pin, uint8_t value) {
	pin.
	*PORT = (*PORT & _BV(pin)) | (value << pin);
}


/**
* @brief 
*
* @param pin
*
* @return 
*/
static inline uint8_t pinRead(GPIO_PIN pin) {
	
}


#endif /*PINOUT_H*/

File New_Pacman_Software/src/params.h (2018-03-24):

#ifndef PARAMS_H
#define PARAMS_H

// standard library includes
#include <stdint.h>
#include "atom.h"
#include "config.h"
#include "atomqueue.h"
#include "atomutils.h"
#include "atomport.h"
#include "atmel/can_lib.h"
#include "atommutex.h"


//SOFTWARE VERSION (based on commit number in gitlab)
#define version 2.2

// LCD values
#define EN_LOW	0x08

#define NUM_CONFIG_PARAMS 12
#define PASSWORD 0xFF
#define NUM_TASKS 8

//watchdog task indices
#define WATCH_I2C 			0
#define WATCH_GUI 			1
#define WATCH_CHARGE 		2
#define WATCH_SAFETY 		3
#define WATCH_CONFIG 		4
#define WATCH_HEART 		5
#define WATCH_CAN 			6
#define WATCH_BUTTON 		7
volatile uint8_t watch_dog_list[NUM_TASKS];
volatile bool pet_dog;
volatile uint8_t wait_counter;



volatile uint8_t config_addr[NUM_CONFIG_PARAMS];


//4 arrays for the 4 lines on the LCD
//displays 1 and 2 are switched (lines will be opposite)
unsigned char display_0[20];
unsigned char display_1[20];
unsigned char display_2[20];
unsigned char display_3[20];

//typedef enum {false,true} bool;  stdbool.h is included in can_lib.h so this is no longer necessary.
typedef enum {boot,chrg,chrgd,lco,flt,dead,rdy} State; //mirrored values in VSCADA
volatile uint8_t fault_code;

//adding 04012017
struct flt_cond {
  uint8_t active;
  uint8_t cond;
  uint8_t area;
  uint16_t val;
};

/* struct display_time { */
/*   uint32_t sys_seconds; */
/*   uint32_t sys_minutes; */
/*   uint32_t sys_hours; */
/*   uint32_t sys_days; */
/* }; */

volatile struct flt_cond flt_cnd;


//various parameters that will be displayed on the LCD
volatile int16_t shunt_voltage;  //part of pack current calc
volatile int16_t pack_voltage;
volatile int32_t pack_current;
volatile int32_t adc_value;
volatile uint8_t prev_pack_SOC;
volatile uint8_t pack_SOC;
volatile int32_t pack_coulombs;
volatile uint16_t cell_V[7];
volatile uint16_t cell_T[7];

volatile uint8_t cell_status[7];
volatile State pack_state;
volatile bool sloop_state;
volatile bool CHRG_DET;
volatile bool LOW_DET;
volatile bool button_enter; // Is always high for some reason
volatile bool button_up;
volatile bool button_down;


//debouncing variables
volatile bool prev_button_up;
volatile bool prev_button_down;
volatile bool prev_button_enter;

volatile uint8_t num_cells;

volatile uint8_t locked;
volatile uint8_t sloop_always_closed;

// NEED TO LOG RECENT STATE TRANSITIONS AND TIMESTAMPS:
volatile State recent_states[5];
volatile uint32_t state_ts[5];
//volatile struct display_time state_ts[5];

volatile uint32_t sleep_time;

volatile uint16_t CANADD_PACKINFO1;
volatile uint16_t CANADD_PACKINFO2;
volatile uint16_t CANADD_CELLINFO;
volatile uint8_t  PACK_NUM;


//Flags for lcd message and bypass selection timing
volatile bool lcd_flag;
volatile bool bypass_flag;

volatile bool lcd_active;

//Calibration factors
#define pack_Voff				-0.3
#define pack_ametes_Aoff  		.6775//amps
#define pack_INA226_Aoff 		-0.00886//amps
#define pack_Vslp				1.014
#define pack_ametes_Aslp 		107.4977// A/V
#define pack_INA226_Aslp		0.9636 //none
volatile uint16_t cell_Voff[7];
volatile uint16_t cell_Toff[7];
volatile uint16_t cell_Vslp[7];
volatile float cell_Tslp[7];


//CAN parameters
// #define CANADD_PACKINFO1  0x0500  //additional packs should be at 0x0510, 0x520, 0x0530
// #define CANADD_PACKINFO2  0x0501  //additional packs should be at 0x0511, 0x521, 0x0531
// #define CANADD_CELLINFO   0x0502  //additional packs should be at 0x0512, 0x522, 0x0532
volatile uint8_t can_buff[8];
st_cmd_t can_frame;
volatile can_ctrl_t can_frame_ctrl;
volatile can_id_t can_frame_id;

//SOC parameters
#define MAX_COULOMBS  216000000 // * 10^-3 coulombs in a full pack

//Mutex to prevent integration of a bad current value
ATOM_MUTEX A_mutex;

//EEPROM Parameters
/* #define DEFAULT_CAN_ADDR1 	0x0500 	 */
/* #define DEFAULT_CAN_ADDR2 	0x0501 	 */
/* #define DEFAULT_CAN_ADDR3 	0x0502 */
#define DEFAULT_PACK_NUM 	0x01
#define DEFAULT_NUM_CELLS       7

#define DEFAULT_MAX_CELL_TEMP 0x3C
#define DEFAULT_MAX_CELL_VOLTAGE 0x28
#define DEFAULT_MIN_CELL_VOLTAGE 0x1B
#define DEFAULT_SCREEN_RESET_TIME 0x0F
#define DEFAULT_SCREEN_SLEEP_TIME 0x78
#define DEFAULT_MAX_CHARGE_CELL_VOLTAGE 0x27
#define DEFAULT_MIN_CURRENT 0x01
#define DEFAULT_SLOOP_ALWAYS_CLOSED 0x00
#define DEFAULT_SET_SOC 50


volatile uint8_t min_cell_voltage;
volatile uint8_t max_cell_voltage;
volatile uint8_t max_charge_cell_voltage;
volatile uint8_t min_current;

volatile uint8_t max_cell_temp;

volatile uint8_t screen_reset_time;
volatile uint8_t screen_sleep_time;


#define EEPROM_SOC  		1		// location in memory of last recorded State of Charge
#define EEPROM_LOCK             2               // location in memory of the lock state
#define EEPROM_MAX_CELL_TEMP    3
#define EEPROM_MAX_CELL_VOLTAGE 4
#define EEPROM_SCREEN_RESET_TIME 5
#define EEPROM_SCREEN_SLEEP_TIME 6
#define EEPROM_PACK_ID          8               // location in memory of the pack id
#define EEPROM_CELL_COUNT       9               // location in memory of the number of cells beign used
#define EEPROM_MIN_CELL_VOLTAGE 10
#define EEPROM_MAX_CHARGE_CELL_VOLTAGE 11
#define EEPROM_MIN_CURRENT 12
#define EEPROM_SLOOP_ALWAYS_CLOSED 13



/* #define EEPROM_CAN_ADDR1	2		// location in memory of CAN address for CANADD_PACKINFO1 */
/* #define EEPROM_CAN_ADDR2	4		// location in memory of CAN address for CANADD_PACKINFO2 */
/* #define EEPROM_CAN_ADDR3	6		// location in memory of CAN address for CANADD_CELLINFO */

/*
#define EEPROM_PACK_V_OFF  	9
#define EEPROM_PACK_V_SLP 	11
#define EEPROM_AMETES_AOFF	13
#define EEPROM_AMETES_ASLP 	15
#define EEPROM_INA226_ASLP 	17
#define EEPROM_INA226_ASLP 	19
*/
#endif

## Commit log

2017-01-31 Pushed rev 0.8 schematic
    [bom.csv, can_xcvr.sch, connectors.sch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]
2017-01-31 Added in annotations about hardware changed
    [can_xcvr.sch, connectors.sch, ftdi_uart.sch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]
2017-04-03 FIGURED IT OUT AND FIXED THE CURRENT PROBLEMS :)
2017-04-04 fixed the bug in new pacman software
    [task_config.c]
2017-04-06 made some updates, including configuring number of cells, fixing pack id set
    [params.h, task_config.c]
2017-04-09 Added new schematic/PCB layout for revised Control Panel; schematic/pcb not yet reviewed by Nadovich.
    [panel pcb-B_Cu.gbr, panel pcb-B_Mask.gbr, panel pcb-B_SilkS.gbr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]
2017-04-10 Added new directory to revert to in case of disaster. Also working on state transition logging. Still needs to be displayed on screen
    [i2c.c]
2017-04-12 trying to fix the enter button
2017-04-13 adding i2c workaround
2017-04-13 added other workaround for soc and i2c
    [task_charge.c]
2017-04-13 adding a workaround for i2c problem for temperature sensor
    [task_config.c]
2017-04-13 workaround for temp and i2c
2017-04-13 saving off new folder with current version of stable, working software
2017-04-13 makefile now preserves eeprom. also if no buttons are pressed, lcd display goes back to main screen
2017-04-17 added risky folder. contains un-tested software. current revision removes fault 3, and revises i2c daq protocol, trying to be more accurate
2017-04-25 lcd display now turns off correctly after 2 minutes of inactivity. Seems to draw ~10mA less
    [i2c.c]
2017-05-04 Added new watchdog frequency for AMS boards.
    [firmware.production.obj]
2017-05-12 Added todos to fix known bugs
    [i2c.c, task_charge.c]
2017-05-16 Fix for display implemented, moved to v0.17
    [params.h]
2018-01-24 Fixed debouncing of buttons. Adding new param for min_cell_voltage
    [params.h, task_config.c]
2018-01-24 Minor bug fix to param max_min cell voltage mixup
    [task_config.c]
2018-01-25 Added two new params. max cell charge voltage and min current
2018-01-25 Started working on fixing the watchdog timer
    [params.h, task_config.c]
2018-01-25 Added watch dog counters to each task after for loop. added reseting code to watchdog
    [params.h, task_charge.c, task_config.c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]
2018-01-25 Fixed bug with for loop
    [params.h]
2018-01-31 Changed condition for lower voltage threshold
2018-02-15 Fixed watchdog bug by taking care of overflow
    [task_charge.c, task_config.c, task_heartbeat.c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]
2018-02-15 Fixed watchdog error. I wasnt resetting the timer
    [params.h, task_charge.c, task_config.c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]
2018-02-22 Updated max cell charge voltasge from 37 to 3700
2018-02-28 Made I2C not necessary for watchdog
2018-03-17 Fixed errors in updated UI
    [params.h]
2018-03-17 Fixed enter button
2018-03-20 Fixed UI display and SOC problem of dropping every time it resets
    [params.h, task_charge.c, task_config.c]
2018-03-23 Changed display during charging
